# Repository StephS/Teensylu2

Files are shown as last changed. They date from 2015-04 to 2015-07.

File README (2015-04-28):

This board is a PROTOTYPE until the design is built and tested.

Version 0.9 is ready for production, earlier versions should not be used.

Please see Teensylu2_Pin_Map.htm for the correct pin mapping using the teensyduino library. Analog pins should use the analog pin reference.

The BOM is included. Please use parts of the same or higher ratings.

If you'd like to donate so I can buy the full version of Eagle, and make more cool stuff, please contact me through Google+

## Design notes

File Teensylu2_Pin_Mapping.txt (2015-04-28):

Package Pin Number	Pin Name	Teensyduino Pin Number	Connected NET	Description
1	PE6	18	Z-STOP	Z Endstop or Z probe input
2	PE7	19	PE7	Not Connected
9	PE3		PE3	Not Connected
10	PB0	20	SDCS	SDCS
11	PB1	21	SCLK	SCLK
12	PB2	22	MOSI	MOSI
13	PB3	23	MISO	MISO
14	PB4	24	PB4	Extension Header PIN 5
15	PB5	25	Y-STOP	Y Endstop
16	PB6	26	X-STOP	X Endstop
17	PB7	27	SCDCD	SD Card Detect
18	PE4	36	E-STOP	E Endstop
19	PE5	37	PE5	Extension Header PIN 4
25	PD0	0	PD0-SCL	Extension Header PIN 6
26	PD1	1	PD1-SDA	Extension Header PIN 7
27	PD2	2	PD2-RX1	Extension Header PIN 8
28	PD3	3	PD3-TX1	Extension Header PIN 9
29	PD4	4	PD4	Extension Header PIN 10
30	PD5	5	PD5	Extension Header PIN 11
31	PD6	6	PD6	Extension Header PIN 12
32	PD7	7	PD7	Extension Header PIN 13
33	PE0	8	E2-STEP	2nd Extruder STEP pin
34	PE1	9	E2-DIR	2nd Extruder DIR pin
35	PC0	10	!E2-ENABLE	2nd Extruder ENABLE pin
36	PC1	11	E1-STEP	1st Extruder STEP pin
37	PC2	12	E1-DIR	1st Extruder DIR pin
38	PC3	13	!E1-ENABLE	1st Extruder ENABLE pin
39	PC4	14	!HOTBED	Hot Bed Mosfet control pin
40	PC5	15	!HOTEND-1	Hot End 1 Mosfet control pin
41	PC6	16	!PWM-FAN	Fan Mosfet control pin
42	PC7	17	Z-STEP	Z Axis STEP pin
43	PE2		PE2	Boot Mode pin
44	PA7	35	Z-DIR	Z Axis DIR pin
45	PA6	34	!Z-ENABLE	Z Axis ENABLE pin
46	PA5	33	Y-STEP	Y Axis STEP pin
47	PA4	32	Y-DIR	Y Axis DIR pin
48	PA3	31	!Y-ENABLE	Y Axis ENABLE pin
49	PA2	30	X-STEP	X Axis STEP pin
50	PA1	29	X-DIR	X Axis DIR pin
51	PA0	28	!X-ENABLE	X Axis ENABLE pin
54	PF7	45	A7	Extension Header PIN 14
55	PF6	44	A6	Not Connected
56	PF5	43	A5	Not Connected
57	PF4	42	A4	Not Connected
58	PF3	41	!HOTEND-2	Hot End 2 Mosfet control pin
59	PF2	40	E2-THERM	Hot End 2 thermistor input pin
60	PF1	39	E1-THERM	Hot End 1 thermistor input pin
61	PF0	38	B-THERM	Hot Bed thermistor input pin

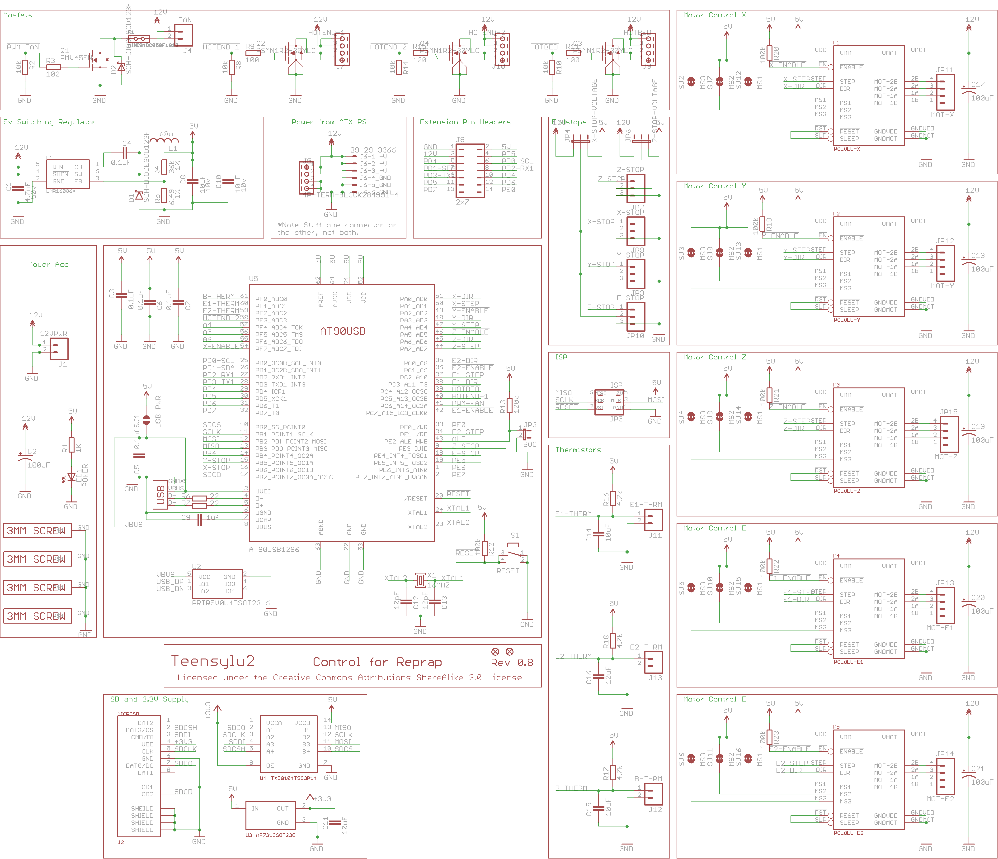
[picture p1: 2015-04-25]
Teensylu2_Schematic.png

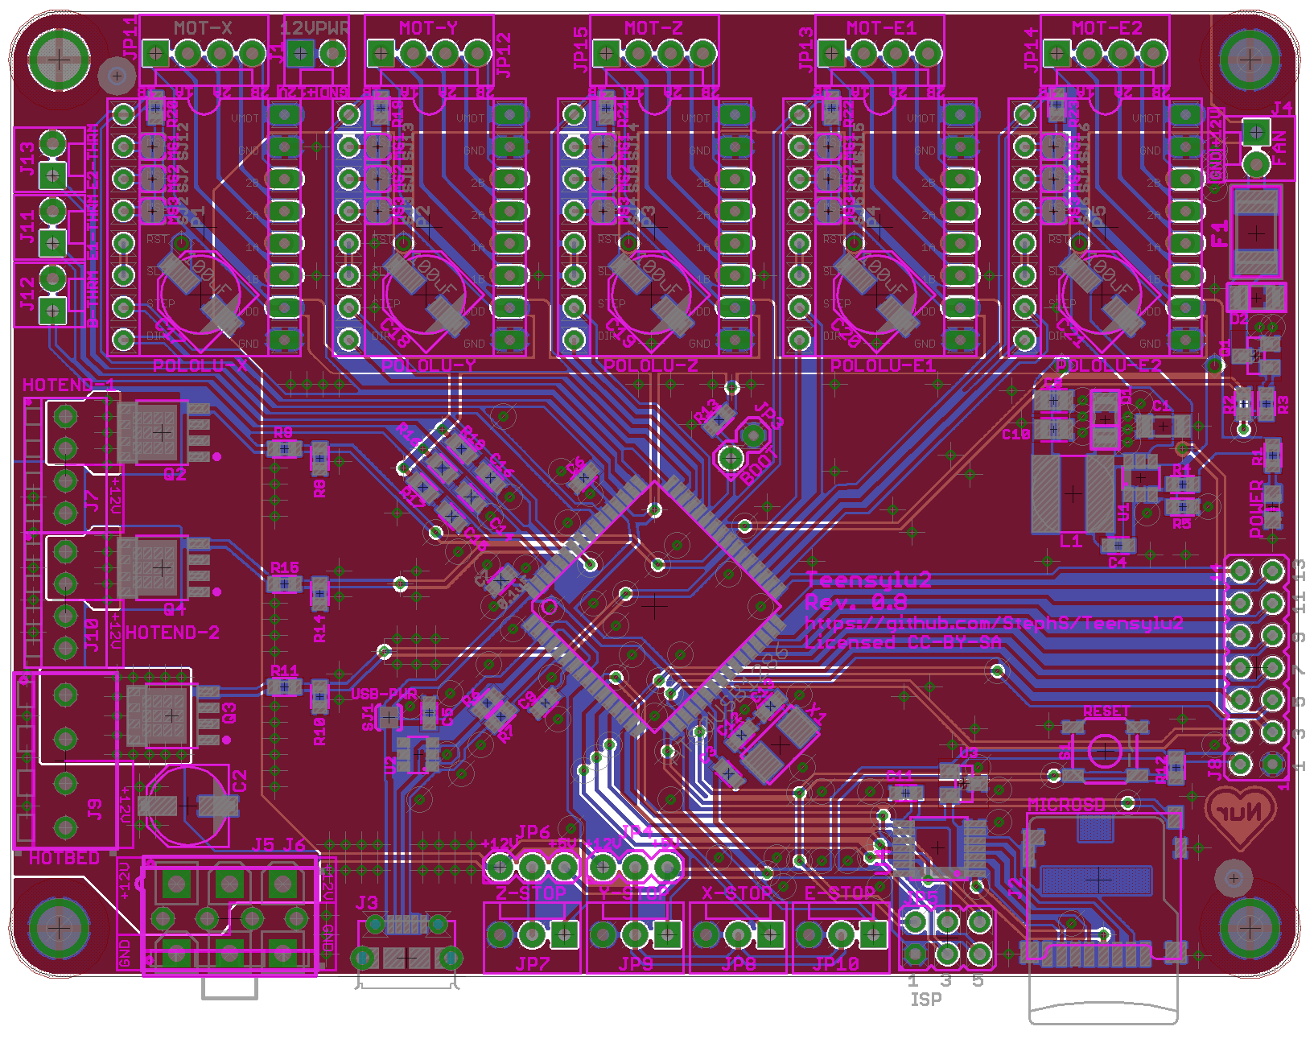
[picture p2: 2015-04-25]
Teensylu2_Board.png

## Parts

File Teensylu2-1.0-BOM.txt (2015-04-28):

Partlist exported from C:/Users/stshalt/Documents/Teensylu2/Teensylu2-0.9.sch at 4/28/2015 11:14:26 AM

Qty Value                 Device                     Package             Parts                             Description                                  CURRENT DCR   DESCRIPTION                      ESR    INDUCTANCE IRMS MANUFACTURER            MANUFACTURER_PART_NUMBER      NOTES                                                                       RDS_ON   REVERSE_VOLTAGE TOLERANCE VDC VGS   VOLTAGE VOLTAGE_OUTPUT
4   0.1uF                 CAPACITOR_0603             CAPC1608X92N        C3, C5, C6, C7                                                                                                                                       Murata                  GRM188R71C104KA01D                                                                                                                 10%       16V                             
1   0.1uF                 CAPACITOR_0603             CAPC1608X92N        C4                                                                                                                                                   Samsung                 CL10B104KB8NNNC                                                                                                                    10%       50V                             
4   100                   RESISTOR_0603              RESC1608X55N        R3, R9, R11, R15                                                                                                                                                                                                                                                                                                                                          
7   100k                  RESISTOR_0603              RESC1608X55N        R12, R13, R19, R20, R21, R22, R23                                                                                                                                                                                                                                                                                                                         
6   100uF                 CPOL-USD                   PANASONIC_D         C2, C17, C18, C19, C20, C21       POLARIZED CAPACITOR, American symbol                                                                               Panasonic               EEE-FTH101XAP                                                                                                                      20%       50v                             
4   10k                   RESISTOR_0603              RESC1608X55N        R2, R8, R10, R14                                                                                                                                                                                                                                                                                                                                          
2   10pF                  CAPACITOR_0603             CAPC1608X92N        C12, C13                                                                                                                                             Samsung                 CL10C100JB8NCNC                                                                                                                    5%        50V                             
4   10uF                  CAPACITOR_0603             CAPC1608X92N        C11, C14, C15, C16                                                                                                                                   Murata                  GRM188R61C106MA73D                                                                                                                 20%       16V                             
2   10uF                  CAPACITOR_0805             CAPC2012X145AN      C8, C10                                                                                                                       0.0030                 Murata                  GRM21BR71A106KE51L                                                                                                                 10%       10v                             
1   16MHZ                 XTAL                       NDK-XTAL            X1                                                                                                                                                   NDK                     NX5032GA-16.000000MHZ-LN-CD-1                                                                                                                                                
1   1K                    RESISTOR_0603              RESC1608X55N        R1                                                                                                                                                                                                                                                                                                                                                        
1   1uF                   CAPACITOR_0603             CAPC1608X92N        C9                                                                                                                                                   Samsung                 CL10A105MO8NNNC                                                                                                                    20%       16V                             
2   22                    RESISTOR_0603              RESC1608X55N        R6, R7                                                                                                                                                                                                                                                                                                                                                    
1   2x7                   JP7Q                       JP7Q                J8                                JUMPER                                                     DIL VERTICAL PC TAIL PIN HEADER                         Harwin                  M20-9980746                                                                                                                                                                  
1   36k                   RESISTOR_0603              RESC1608X55N        R4                                                                                                                                                                                                                                                                                                              1%                                        
1   39-29-3066            39-29-3066                 39-29-3066          J6                                Mini FIT connector 6 pol Without Snap-in peg                                                                       Molex                   0039293066                                                                                                                                                                   
4   3MM-SCREW             3MM-SCREW                  PLATEDSCREW         SCREW1, SCREW2, SCREW3, SCREW4    3mm Plated Through Hole Screw                                                                                                                                                                                                                                                                                           
3   4.7k                  RESISTOR_0603              RESC1608X55N        R16, R17, R18                                                                                                                                                                                                                                                                                                                                             
1   4.7uF                 CAPACITOR_1206             CAPC3215X168N       C1                                                                                                                                                   Yaiyo Yuden             UMK316AB7475KL-T                                                                                                                   10%       50v                             
1   4P-TERM-BLOCK284391-4 4P-TERM-BLOCK284391-4      284391-4            J5                                                                             12A                                                                   TE Connectivity         284391-4                                                                                                                                                                     
1   6.49k                 RESISTOR_0603              RESC1608X55N        R5                                                                                                                                                                                                                                                                                                              1%                                        
1   68uH                  INDUCTORSRN6045            SRN6045             L1                                                                             900mA   0.351                                         68uH       0.9A Bourns                  SRN6045-680M                                                                                                                                                                 
1   AP7313SOT23C          AP7313SOT23C               SOT23C              U3                                                                             150mA         IC REG LDO 3.3V 0.15A SOT23-3                           Diodes Incorporated     AP7313-33SAG-7                                                                                                                                                 3.3V          
1   AT90USB1286           AT90USB                    TQFP64-2            U5                                                                                                                                                   Atmel                   AT90USB1286                                                                                                                                                                  
1   BOOT                  JUMPER-2PTH                1X02                JP3                               Jumper                                                     SIL VERTICAL PC TAIL PIN HEADER                         Harwin                  M20-9990246                                                                                                                                                                  
2   FIDUCIAL1X2.5         FIDUCIAL1X2.5              FIDUCIAL-1X2.5      JP1, JP2                          Fiducial Alignment Points                                                                                                                                                                                                                                                                                               
1   HOTBED                4P-TERM-BLOCK284391-4      284391-4            J9                                                                             12A                                                                   TE Connectivity         284391-4                                                                                                                                                                     
1   HOTEND-1              4P-TERM-BLOCK282834-4      282834-4            J7                                                                             10A                                                                   TE Connectivity         282834-4                                                                                                                                                                     
1   HOTEND-2              4P-TERM-BLOCK282834-4      282834-4            J10                                                                            10A                                                                   TE Connectivity         282834-4                                                                                                                                                                     
1   ISP                   PROGHEADER                 ISP                 JP5                               JUMPER                                                                                                                                                                                                                                                                                                                  
2   JUMPER-3PTH           JUMPER-3PTH                1X03                JP4, JP6                                                                                                                                                                                                                                                                                                                                                  
1   LMR16006X             LMR16006X                  TSOT6               U1                                Texas Instruments LMR16006XDDCT              600mA                                                                 Texas Instruments       LMR16006XDDCT                                                                                                                                                                
5   M02POLAR              M02POLAR                   MOLEX-1X2           J1, J4, J11, J12, J13             Header 2                                                   CONN HEADER 2POS .100 VERT TIN                          Molex                   0022272021                    Can use alternative part for Right Angle. MFG: TE Connectivity PN: 640455-2                                                                    
4   M03POLAR              M03POLAR                   MOLEX-1X3           JP7, JP8, JP9, JP10               Header 3                                                   CONN HEADER 3POS .100 VERT TIN                          Molex                   0022272031                    Can use alternative part for Right Angle. MFG: TE Connectivity PN: 640455-3                                                                    
1   MICROSD               MICROSD                    AMPHENOL-MICROSD    J2                                                                                           CONN MICRO SD CARD PUSH-PULL R/A                        Amphenol                114-00841-68                                                                                                                                                                 
1   MINISMDC050F1812      MINISMDC050F1812           MINISMDC            F1                                                                             0.5A                                                                  TE Connectivity         MINISMDC050F-2                                                                                                                                                               
1   MMUN2211LT3G          TRANSISTOR_NPN_BIASSOT23C  SOT23C              Q5                                Transistor NPN                                             TRANS PREBIAS NPN 246MW SOT23-3                         ON Semiconductor        MMUN2211LT3G                                                                                                                                                                 
1   MOT-E1                M04POLAR                   MOLEX-1X4           JP13                              Header 4                                                   CONN HEADER 4POS .100 VERT TIN                          Molex                   0022272041                    Can use alternative part for Right Angle. MFG: TE Connectivity PN: 640455-4                                                                    
1   MOT-E2                M04POLAR                   MOLEX-1X4           JP14                              Header 4                                                   CONN HEADER 4POS .100 VERT TIN                          Molex                   0022272041                    Can use alternative part for Right Angle. MFG: TE Connectivity PN: 640455-4                                                                    
1   MOT-X                 M04POLAR                   MOLEX-1X4           JP11                              Header 4                                                   CONN HEADER 4POS .100 VERT TIN                          Molex                   0022272041                    Can use alternative part for Right Angle. MFG: TE Connectivity PN: 640455-4                                                                    
1   MOT-Y                 M04POLAR                   MOLEX-1X4           JP12                              Header 4                                                   CONN HEADER 4POS .100 VERT TIN                          Molex                   0022272041                    Can use alternative part for Right Angle. MFG: TE Connectivity PN: 640455-4                                                                    
1   MOT-Z                 M04POLAR                   MOLEX-1X4           JP15                              Header 4                                                   CONN HEADER 4POS .100 VERT TIN                          Molex                   0022272041                    Can use alternative part for Right Angle. MFG: TE Connectivity PN: 640455-4                                                                    
5   MS1                   SOLDERJUMPER-NCSJ-TRACE    SJ_2S-TRACE         SJ12, SJ13, SJ14, SJ15, SJ16                                                                                                                                                                                                                                                                                                                              
5   MS2                   SOLDERJUMPER-NCSJ-TRACE    SJ_2S-TRACE         SJ7, SJ8, SJ9, SJ10, SJ11                                                                                                                                                                                                                                                                                                                                 
5   MS3                   SOLDERJUMPER-NCSJ-TRACE    SJ_2S-TRACE         SJ2, SJ3, SJ4, SJ5, SJ6                                                                                                                                                                                                                                                                                                                                   
1   PMV45EN               MOSFET-NCH_SOT-23          SOT23C              Q1                                                                             1.2A                                                                  International Rectifier IRLML2060TRPBF                                                                                                                                         60V                   
1   POLOLU-E1             POLOLU-ALLEGRO             POLOLU-STEPPER-PTH  P4                                                                                                                                                                                                                                                                                                                                                        
1   POLOLU-E2             POLOLU-ALLEGRO             POLOLU-STEPPER-PTH  P5                                                                                                                                                                                                                                                                                                                                                        
1   POLOLU-X              POLOLU-ALLEGRO             POLOLU-STEPPER-PTH  P1                                                                                                                                                                                                                                                                                                                                                        
1   POLOLU-Y              POLOLU-ALLEGRO             POLOLU-STEPPER-PTH  P2                                                                                                                                                                                                                                                                                                                                                        
1   POLOLU-Z              POLOLU-ALLEGRO             POLOLU-STEPPER-PTH  P3                                                                                                                                                                                                                                                                                                                                                        
1   POWER                 LEDCHIPLED_0805            CHIPLED_0805        LED1                              LED                                                                                                                Kingbright              APT2012SGC                                                                                                                                                                   
1   PRTR5V0U4DSOT23-6     PRTR5V0U4DSOT23-6          SOT23-6             U2                                NXP Semiconductors PRTR5V0U4D,125                                                                                  NXP Semiconductors      PRTR5V0U4D,125                                                                                                                                                               
3   PSMN1R2-30YLC         PSMN1R2-30YLCPOWERPACK-S08 LFPACK-POWERPAK-SO8 Q2, Q3, Q4                        N-Channel MOSFET - 30V 100A LFPAK            100A                                                                  NXP Semiconductors      PSMN1R2-30YLC,115                                                                                         1.25mOhm                               1.95V 30V                   
1   RESET                 TAC_SWITCHSMD              TACTILE_SWITCH_SMD  S1                                Momentary Switch                                                                                                   Bourns                  7914J-1-000E                                                                                                                                                                 
2   SCH-DIODESOD123F      SCH-DIODESOD123F           SOD123F             D1, D2                            Schottky Diodes                              1A                                                                    NXP Semiconductors      PMEG4010CEH,115                                                                                                    40V                                                       
1   TXB0104TSSOP14        TXB0104TSSOP14             TSSOP14             U4                                                                                           IC VOLT-LEVEL TRANSLATOR 14TSSOP                        Texas Instruments       TXB0104PWR                                                                                                                                                                   
1   USB-MICRO-PTH         USB-MICRO-PTH              USB-MICROB-PTH      J3                                USB Connectors                                                                                                     FCI                     10118194-0001LF                                                                                                                                                              
1   USB-PWR               SOLDERJUMPERNO             SJ_2S-NO            SJ1                               Solder Jumper

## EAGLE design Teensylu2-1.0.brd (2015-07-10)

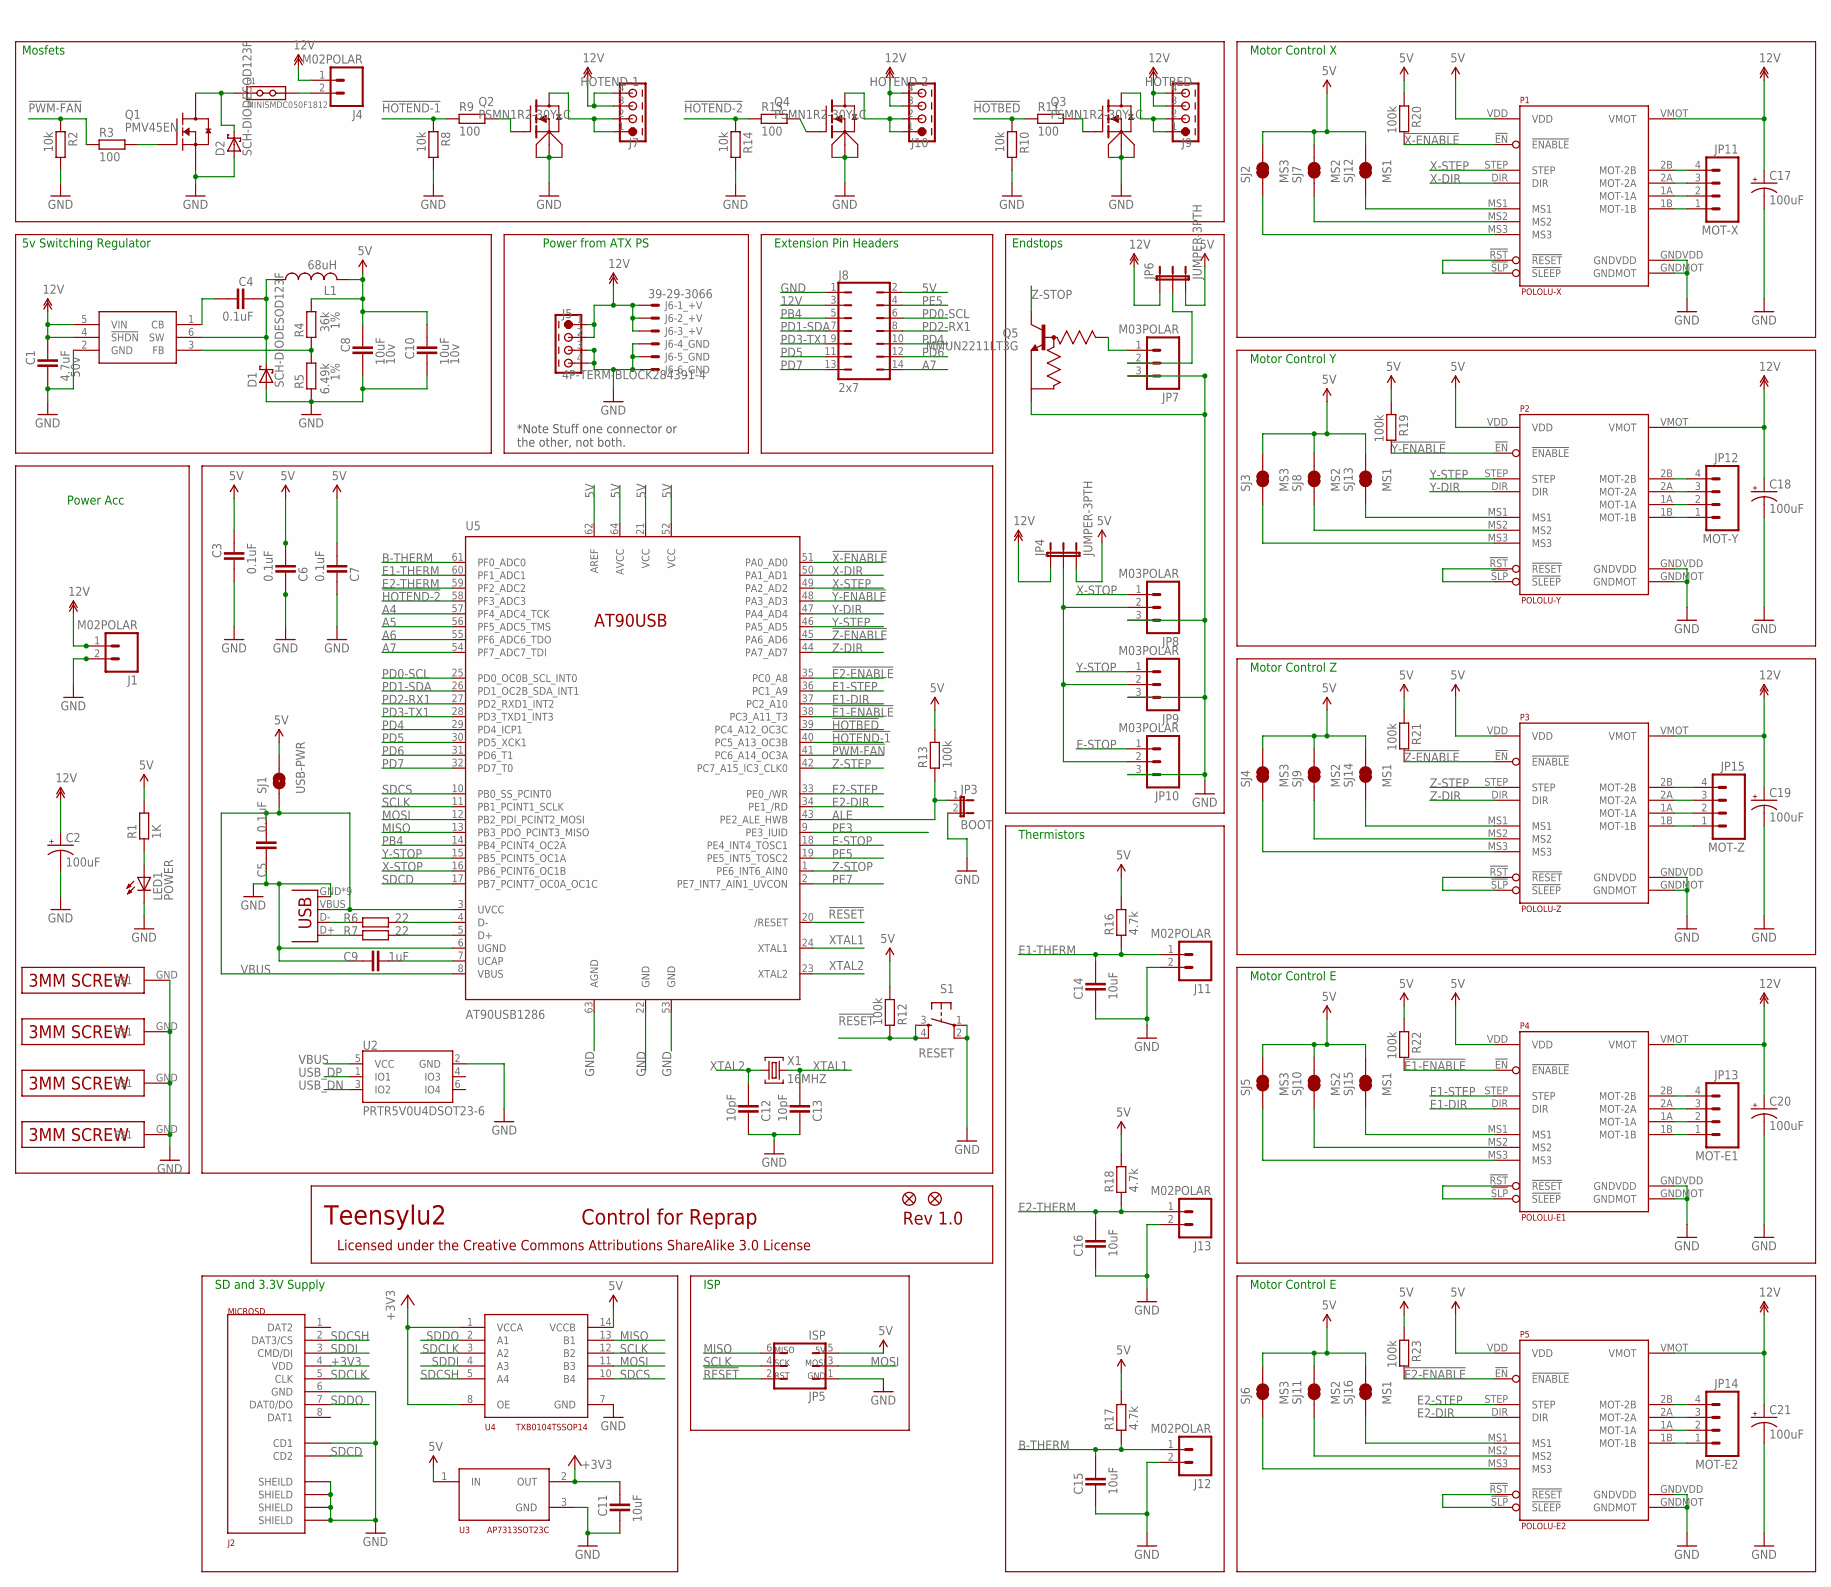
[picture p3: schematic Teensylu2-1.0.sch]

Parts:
C1: 4.7uF; CAPC3215X168N; TOLERANCE 10%; MANUFACTURER_PART_NUMBER UMK316AB7475KL-T
C2, C17, C18, C19, C20, C21: 100uF; PANASONIC_D; TOLERANCE 20%; MANUFACTURER_PART_NUMBER EEE-FTH101XAP
C3, C5, C6, C7: 0.1uF; CAPC1608X92N; TOLERANCE 10%; MANUFACTURER_PART_NUMBER GRM188R71C104KA01D
C4: 0.1uF; CAPC1608X92N; TOLERANCE 10%; MANUFACTURER_PART_NUMBER CL10B104KB8NNNC
C8, C10: 10uF; CAPC2012X145AN; TOLERANCE 10%; MANUFACTURER_PART_NUMBER GRM21BR71A106KE51L
C9: 1uF; CAPC1608X92N; TOLERANCE 20%; MANUFACTURER_PART_NUMBER CL10A105MO8NNNC
C11, C14, C15, C16: 10uF; CAPC1608X92N; TOLERANCE 20%; MANUFACTURER_PART_NUMBER GRM188R61C106MA73D
C12, C13: 10pF; CAPC1608X92N; TOLERANCE 5%; MANUFACTURER_PART_NUMBER CL10C100JB8NCNC
D1: SCH-DIODESOD123F; SOD123F; MANUFACTURER_PART_NUMBER PMEG4010CEH,115
D2: SCH-DIODESOD123F; SOD123F
F1: MINISMDC050F1812; MINISMDC
J1, J4, J11, J12, J13: M02POLAR; MOLEX-1X2; MANUFACTURER_PART_NUMBER 0022272021
J2: MICROSD; AMPHENOL-MICROSD
J3: USB-MICRO-PTH; USB-MICROB-PTH
J5: 4P-TERM-BLOCK284391-4; 284391-4
J6: 39-29-3066
J7: HOTEND-1; 282834-4
J8: 2x7; JP7Q; MANUFACTURER_PART_NUMBER M20-9980746
J9: HOTBED; 284391-4
J10: HOTEND-2; 282834-4
JP1, JP2: FIDUCIAL1X2.5; FIDUCIAL-1X2.5
JP3: BOOT; 1X02; MANUFACTURER_PART_NUMBER M20-9990246
JP4, JP6: JUMPER-3PTH; 1X03
JP5: ISP
JP7, JP8, JP9, JP10: M03POLAR; MOLEX-1X3; MANUFACTURER_PART_NUMBER 0022272031
JP11: MOT-X; MOLEX-1X4
JP12: MOT-Y; MOLEX-1X4
JP13: MOT-E1; MOLEX-1X4
JP14: MOT-E2; MOLEX-1X4
JP15: MOT-Z; MOLEX-1X4
L1: 68uH; SRN6045; MANUFACTURER_PART_NUMBER SRN6045-680M
LED1: POWER; CHIPLED_0805; MANUFACTURER_PART_NUMBER APT2012SGC
P1: POLOLU-X; POLOLU-STEPPER-PTH
P2: POLOLU-Y; POLOLU-STEPPER-PTH
P3: POLOLU-Z; POLOLU-STEPPER-PTH
P4: POLOLU-E1; POLOLU-STEPPER-PTH
P5: POLOLU-E2; POLOLU-STEPPER-PTH
Q1: PMV45EN; SOT23C; VOLTAGE 60V; MANUFACTURER_PART_NUMBER IRLML2060TRPBF
Q2, Q3, Q4: PSMN1R2-30YLC; LFPACK-POWERPAK-SO8
Q5: MMUN2211LT3G; SOT23C; MANUFACTURER_PART_NUMBER MMUN2211LT3G
R1: 1K; RESC1608X55N
R2, R8, R10, R14: 10k; RESC1608X55N
R3, R9, R11, R15: 100; RESC1608X55N
R4: 36k; RESC1608X55N; TOLERANCE 1%
R5: 6.49k; RESC1608X55N; TOLERANCE 1%
R6, R7: 22; RESC1608X55N
R12, R13, R19, R20, R21, R22, R23: 100k; RESC1608X55N
R16, R17, R18: 4.7k; RESC1608X55N
S1: RESET; TACTILE_SWITCH_SMD
SCREW1, SCREW2, SCREW3, SCREW4: 3MM-SCREW; PLATEDSCREW
SJ1: USB-PWR; SJ_2S-NO
SJ2, SJ3, SJ4, SJ5, SJ6: MS3; SJ_2S-TRACE
SJ7, SJ8, SJ9, SJ10, SJ11: MS2; SJ_2S-TRACE
SJ12, SJ13, SJ14, SJ15, SJ16: MS1; SJ_2S-TRACE
U1: LMR16006X; TSOT6
U2: PRTR5V0U4DSOT23-6; SOT23-6
U3: AP7313SOT23C; SOT23C
U4: TXB0104TSSOP14; TSSOP14
U5: AT90USB1286; TQFP64-2; MANUFACTURER_PART_NUMBER AT90USB1286
X1: 16MHZ; NDK-XTAL; MANUFACTURER_PART_NUMBER NX5032GA-16.000000MHZ-LN-CD-1

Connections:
5V: C3.1, C6.2, C7.2, C8.1, C10.1, J8.2, JP4.3, JP5.5, JP6.3, L1.2, P1.VDD, P2.VDD, P3.VDD, P4.VDD, P5.VDD, R1.2, R4.1, R12.2, R13.2, R16.2, R17.2, R18.2, R19.1, R20.1, R21.1, R22.1, R23.1, SJ1.2, SJ2.2, SJ3.2, SJ4.2, SJ5.2, SJ6.2, SJ7.2, SJ8.2, SJ9.2, SJ10.2, SJ11.2, SJ12.2, SJ13.2, SJ14.2, SJ15.2, SJ16.2, U3.1 (IN), U4.14 (VCCB), U5.21 (VCC), U5.52 (VCC), U5.62 (AREF), U5.64 (AVCC)
5VREG_CB: C4.2, U1.1 (CB)
5VREG_FB: R4.2, R5.1, U1.3 (FB)
5VREG_SW: C4.1, D1.C, L1.1, U1.6 (SW)
12V: C1.1, C2.+, C17.+, C18.+, C19.+, C20.+, C21.+, J1.1, J4.1, J5.1, J5.2, J6.1, J6.2, J6.3, J7.3, J7.4, J8.3, J9.3, J9.4, J10.3, J10.4, JP4.1, JP6.1, P1.VMOT, P2.VMOT, P3.VMOT, P4.VMOT, P5.VMOT, U1.4 (!SHDN), U1.5 (VIN)
!E1-ENABLE: P4.!EN (!ENABLE), R22.2, U5.38 (PC3_A11_T3)
!E2-ENABLE: P5.!EN (!ENABLE), R23.2, U5.35 (PC0_A8)
!HOTBED: R10.1, R11.1, U5.39 (PC4_A12_OC3C)
!HOTEND-1: R8.1, R9.1, U5.40 (PC5_A13_OC3B)
!HOTEND-2: R14.1, R15.1, U5.58 (PF3_ADC3)
!PWM-FAN: R2.1, R3.1, U5.41 (PC6_A14_OC3A)
!RESET: JP5.2, R12.1, S1.3, S1.4, U5.20 (/RESET)
!X-ENABLE: P1.!EN (!ENABLE), R20.2, U5.51 (PA0_AD0)
!Y-ENABLE: P2.!EN (!ENABLE), R19.2, U5.48 (PA3_AD3)
!Z-ENABLE: P3.!EN (!ENABLE), R21.2, U5.45 (PA6_AD6)
+3V3: C11.1, J2.4 (VDD), U3.2 (OUT), U4.1 (VCCA), U4.8 (OE)
A4: U5.57 (PF4_ADC4_TCK)
A5: U5.56 (PF5_ADC5_TMS)
A6: U5.55 (PF6_ADC6_TDO)
A7: J8.14, U5.54 (PF7_ADC7_TDI)
ALE: JP3.1, R13.1, U5.43 (PE2_ALE_HWB)
B-THERM: C15.2, J12.1, R17.1, U5.61 (PF0_ADC0)
E1-DIR: P4.DIR, U5.37 (PC2_A10)
E1-STEP: P4.STEP, U5.36 (PC1_A9)
E1-THERM: C14.2, J11.1, R16.1, U5.60 (PF1_ADC1)
E2-DIR: P5.DIR, U5.34 (PE1_/RD)
E2-MOT-1A: JP14.2, P5.1A (MOT-1A)
E2-MOT-1B: JP14.1, P5.1B (MOT-1B)
E2-MOT-2A: JP14.3, P5.2A (MOT-2A)
E2-MOT-2B: JP14.4, P5.2B (MOT-2B)
E2-STEP: P5.STEP, U5.33 (PE0_/WR)
E2-THERM: C16.2, J13.1, R18.1, U5.59 (PF2_ADC2)
E-MOT-1A: JP13.2, P4.1A (MOT-1A)
E-MOT-1B: JP13.1, P4.1B (MOT-1B)
E-MOT-2A: JP13.3, P4.2A (MOT-2A)
E-MOT-2B: JP13.4, P4.2B (MOT-2B)
E-MS1: P4.MS1, SJ15.1
E-MS2: P4.MS2, SJ10.1
E-MS3: P4.MS3, SJ5.1
E-MS4: P5.MS1, SJ16.1
E-MS5: P5.MS2, SJ11.1
E-MS6: P5.MS3, SJ6.1
E-RESETSLEEP: P4.!RST (!RESET), P4.!SLP (!SLEEP)
E-RESETSLEEP1: P5.!RST (!RESET), P5.!SLP (!SLEEP)
E-STOP: JP10.1, U5.18 (PE4_INT4_TOSC1)
ENDSTOP+V: JP4.2, JP8.2, JP9.2, JP10.2
GND: C1.2, C2.-, C3.2, C5.1, C6.1, C7.1, C8.2, C9.1, C10.2, C11.2, C12.1, C13.1, C14.1, C15.1, C16.1, C17.-, C18.-, C19.-, C20.-, C21.-, D1.A, D2.A, J1.2, J2.6 (GND), J2.C1 (SHEILD), J2.C2 (SHIELD), J2.C3 (SHIELD), J2.C4 (SHIELD), J2.CD1, J3.GND, J3.GND1 (GND), J3.GND2 (GND), J3.GND3 (GND), J3.GND4 (GND), J3.GND5 (GND), J3.GND6 (GND), J3.GND7 (GND), J3.GND8 (GND), J5.3, J5.4, J6.4, J6.5, J6.6, J8.1, J11.2, J12.2, J13.2, JP3.2, JP5.1, JP7.3, JP8.3, JP9.3, JP10.3, LED1.C, P1.GNDMOT, P1.GNDVDD, P2.GNDMOT, P2.GNDVDD, P3.GNDMOT, P3.GNDVDD, P4.GNDMOT, P4.GNDVDD, P5.GNDMOT, P5.GNDVDD, Q1.2 (S), Q2.1 (S1), Q2.2 (S2), Q2.3 (S3), Q3.1 (S1), Q3.2 (S2), Q3.3 (S3), Q4.1 (S1), Q4.2 (S2), Q4.3 (S3), Q5.2 (E), R2.2, R5.2, R8.2, R10.2, R14.2, S1.1, S1.2, SCREW1.GND, SCREW2.GND, SCREW3.GND, SCREW4.GND, U1.2 (GND), U2.2 (GND), U3.3 (GND), U4.7 (GND), U5.6 (UGND), U5.22 (GND), U5.53 (GND), U5.63 (AGND)
HOTBED-GND: J9.1, J9.2, Q3.5-8 (D)
HOTEND-GND: J7.1, J7.2, Q2.5-8 (D)
HOTEND-GND1: J10.1, J10.2, Q4.5-8 (D)
MISO: JP5.6, U4.13 (B1), U5.13 (PB3_PDO_PCINT3_MISO)
MOSI: JP5.3, U4.11 (B3), U5.12 (PB2_PDI_PCINT2_MOSI)
unnamed: LED1.A, R1.1
unnamed: Q3.4 (G), R11.2
unnamed: R6.2, U5.4 (D-)
unnamed: R7.2, U5.5 (D+)
unnamed: F1.P$2, J4.2
unnamed: D2.C, F1.P$1, Q1.3 (D)
unnamed: Q1.1 (G), R3.2
unnamed: Q2.4 (G), R9.2
unnamed: Q4.4 (G), R15.2
PB4: J8.5, U5.14 (PB4_PCINT4_OC2A)
PD0-SCL: J8.6, U5.25 (PD0_OC0B_SCL_INT0)
PD1-SDA: J8.7, U5.26 (PD1_OC2B_SDA_INT1)
PD2-RX1: J8.8, U5.27 (PD2_RXD1_INT2)
PD3-TX1: J8.9, U5.28 (PD3_TXD1_INT3)
PD4: J8.10, U5.29 (PD4_ICP1)
PD5: J8.11, U5.30 (PD5_XCK1)
PD6: J8.12, U5.31 (PD6_T1)
PD7: J8.13, U5.32 (PD7_T0)
PE3: U5.9 (PE3_IUID)
PE5: J8.4, U5.19 (PE5_INT5_TOSC2)
PE7: U5.2 (PE7_INT7_AIN1_UVCON)
SCLK: JP5.4, U4.12 (B2), U5.11 (PB1_PCINT1_SCLK)
SDCD: J2.CD2, U5.17 (PB7_PCINT7_OC0A_OC1C)
SDCLK: J2.5 (CLK), U4.3 (A2)
SDCS: U4.10 (B4), U5.10 (PB0_SS_PCINT0)
SDCSH: J2.2 (DAT3/CS), U4.5 (A4)
SDDI: J2.3 (CMD/DI), U4.4 (A3)
SDDO: J2.7 (DAT0/DO), U4.2 (A1)
UCAP: C9.2, U5.7 (UCAP)
USB_DN: J3.D-, R6.1, U2.3 (IO2)
USB_DP: J3.D+, R7.1, U2.1 (IO1)
VBUS: C5.2, J3.VBUS, SJ1.1, U2.5 (VCC), U5.3 (UVCC), U5.8 (VBUS)
X-DIR: P1.DIR, U5.50 (PA1_AD1)
X-MOT-1A: JP11.2, P1.1A (MOT-1A)
X-MOT-1B: JP11.1, P1.1B (MOT-1B)
X-MOT-2A: JP11.3, P1.2A (MOT-2A)
X-MOT-2B: JP11.4, P1.2B (MOT-2B)
X-MS1: P1.MS1, SJ12.1
X-MS2: P1.MS2, SJ7.1
X-MS3: P1.MS3, SJ2.1
X-RESETSLEEP: P1.!RST (!RESET), P1.!SLP (!SLEEP)
X-STEP: P1.STEP, U5.49 (PA2_AD2)
X-STOP: JP8.1, U5.16 (PB6_PCINT6_OC1B)
XTAL1: C13.2, U5.24 (XTAL1), X1.P$2 (2)
XTAL2: C12.2, U5.23 (XTAL2), X1.P$1 (1)
Y-DIR: P2.DIR, U5.47 (PA4_AD4)
Y-MOT-1A: JP12.2, P2.1A (MOT-1A)
Y-MOT-1B: JP12.1, P2.1B (MOT-1B)
Y-MOT-2A: JP12.3, P2.2A (MOT-2A)
Y-MOT-2B: JP12.4, P2.2B (MOT-2B)
Y-MS1: P2.MS1, SJ13.1
Y-MS2: P2.MS2, SJ8.1
Y-MS3: P2.MS3, SJ3.1
Y-RESETSLEEP: P2.!RST (!RESET), P2.!SLP (!SLEEP)
Y-STEP: P2.STEP, U5.46 (PA5_AD5)
Y-STOP: JP9.1, U5.15 (PB5_PCINT5_OC1A)
Z-DIR: P3.DIR, U5.44 (PA7_AD7)
Z-MOT-1A: JP15.2, P3.1A (MOT-1A)
Z-MOT-1B: JP15.1, P3.1B (MOT-1B)
Z-MOT-2A: JP15.3, P3.2A (MOT-2A)
Z-MOT-2B: JP15.4, P3.2B (MOT-2B)
Z-MS1: P3.MS1, SJ14.1
Z-MS2: P3.MS2, SJ9.1
Z-MS3: P3.MS3, SJ4.1
Z-RESETSLEEP: P3.!RST (!RESET), P3.!SLP (!SLEEP)
Z-STEP: P3.STEP, U5.42 (PC7_A15_IC3_CLK0)
Z-STOP: Q5.3 (C), U5.1 (PE6_INT6_AIN0)
Z-STOP-BIAS: JP7.1, Q5.1 (B)
Z-STOP-SUPPLY: JP6.2, JP7.2

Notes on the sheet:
Motor Control X
Motor Control Y
Motor Control Z
Motor Control E
ISP
Thermistors
Endstops
Mosfets
Power Acc
Teensylu2
Rev 1.0
Control for Reprap
Licensed under the Creative Commons Attributions ShareAlike 3.0 License
Extension Pin Headers
Power from ATX PS
5v Switching Regulator
SD and 3.3V Supply
*Note Stuff one connector or the other, not both.

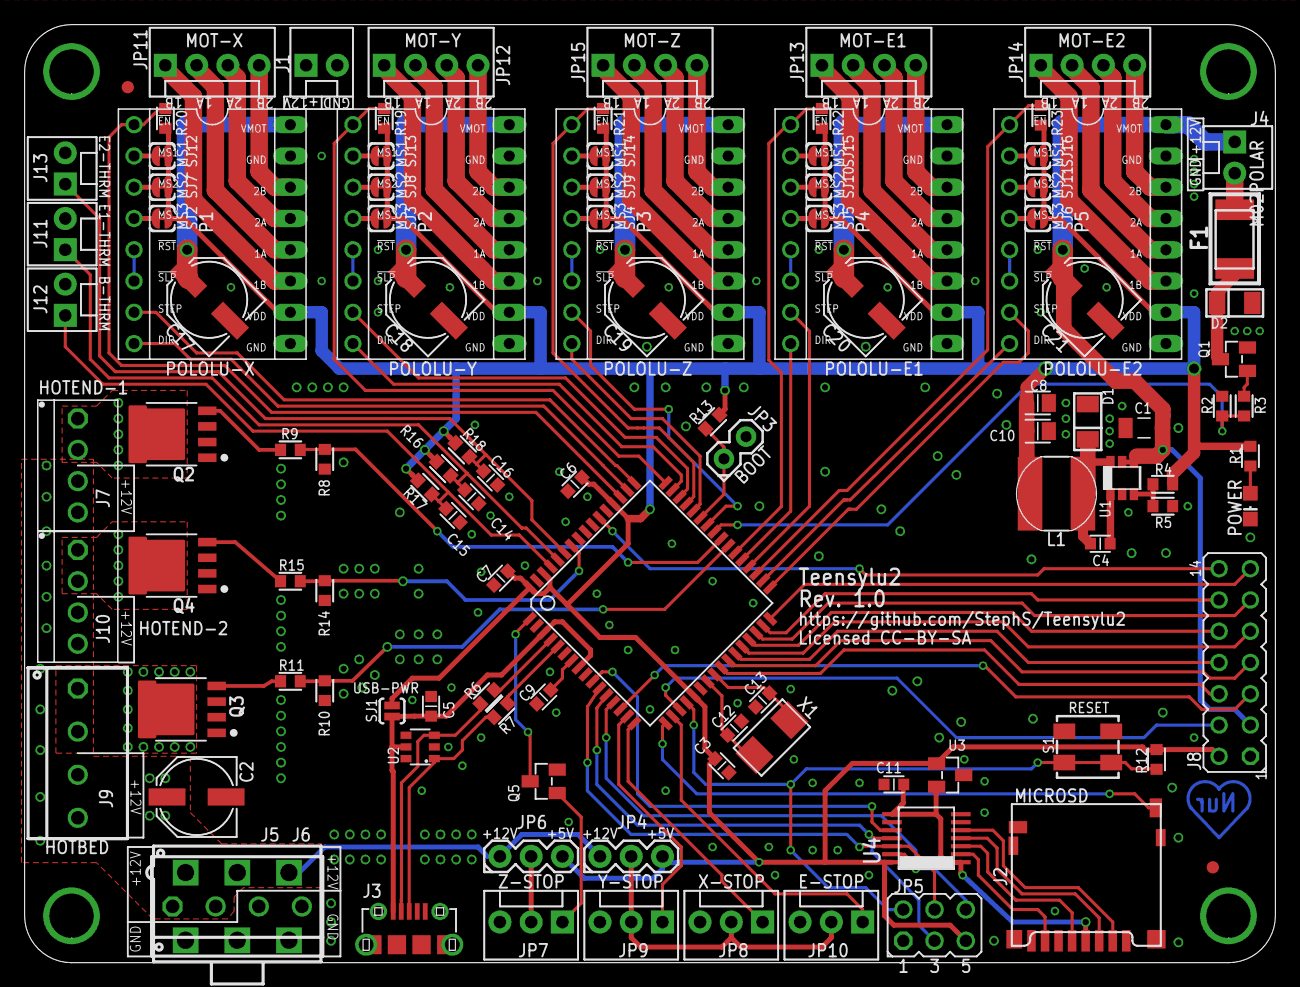
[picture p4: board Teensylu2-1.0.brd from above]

Board: 2 copper layers, 101.6 x 76.2 mm, 114 parts (0 on the bottom side), 116 nets.

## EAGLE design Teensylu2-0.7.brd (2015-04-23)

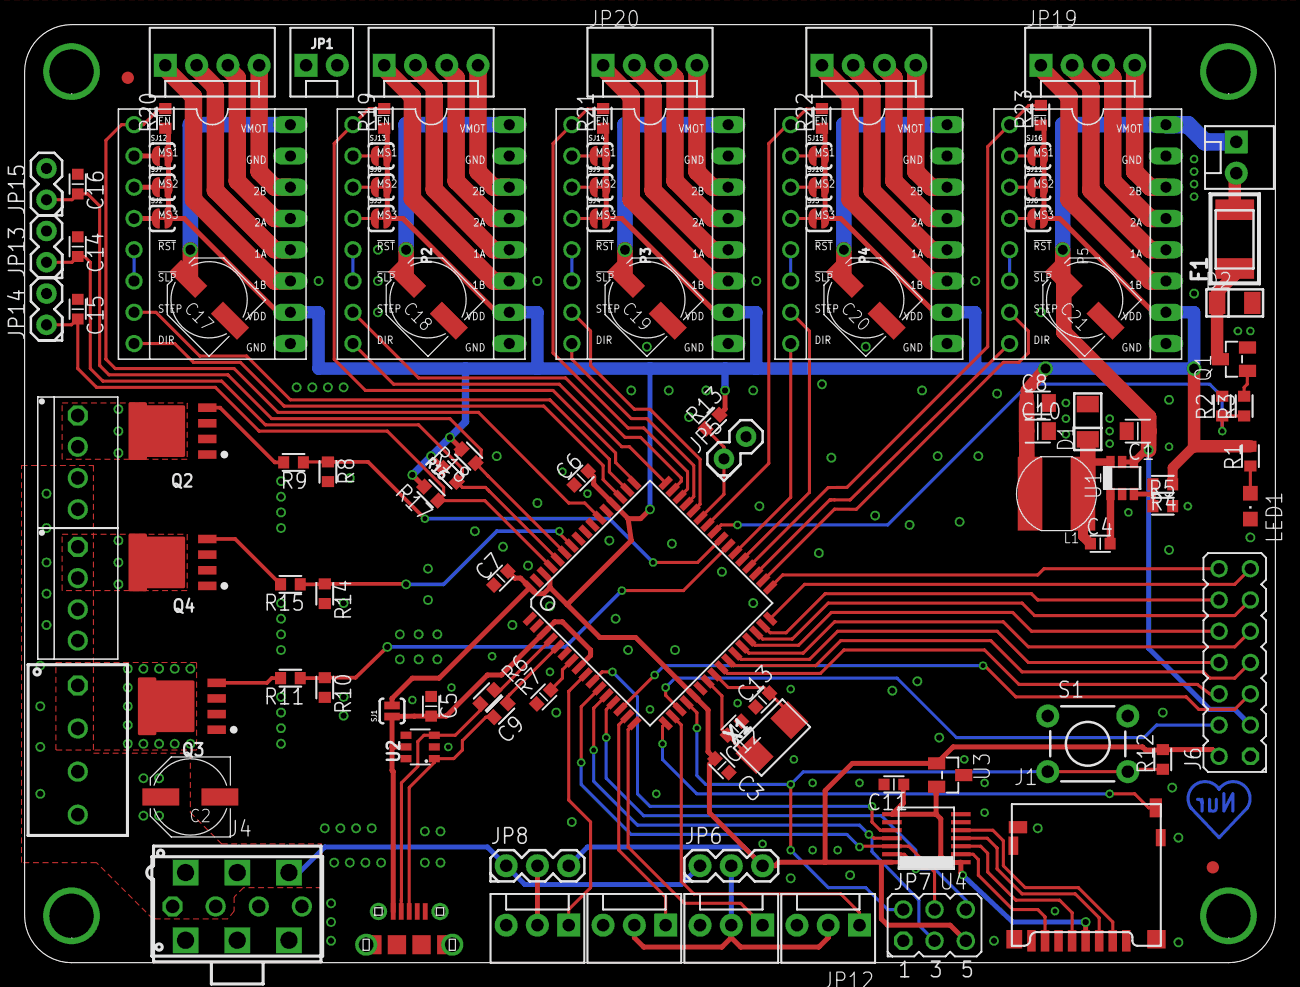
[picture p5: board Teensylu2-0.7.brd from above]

Board: 2 copper layers, 101.6 x 76.2 mm, 113 parts (0 on the bottom side), 115 nets.

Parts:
C1: 4.7uF; CAPC2012X145AN
C2, C17, C18, C19, C20, C21: 100uF; PANASONIC_D
C3, C6, C7: 0.1uF; CAPC1608X92N
C4: 100nF; CAPC1608X92N
C5: 0.1uf; CAPC1608X92N
C8, C10: 10uF; CAPC2012X145AN
C9: 1uf; CAPC1608X92N
C11, C14, C15, C16: 10uF; CAPC1608X92N
C12, C13: 10pF; CAPC1608X92N
D1, D2: SCH-DIODESOD123F; SOD123F
F1: MINISMDC050F1812; MINISMDC
IC1: AT90USB1286; TQFP64-2
J1: MICROSD; AMPHENOL-MICROSD
J2: USB-MICRO-PTH; USB-MICROB-PTH
J3, J7: 4P-TERM-BLOCK284391-4; 284391-4
J4: 39-29-3066
J5, J8: 4P-TERM-BLOCK282834-4; 282834-4
J6: 2x7; JP7Q
JP1: 12VPWR; MOLEX-1X2
JP2: FAN; MOLEX-1X2
JP3, JP4: FIDUCIAL1X2.5; FIDUCIAL-1X2.5
JP5: BOOT; 1X02
JP6, JP8: JUMPER-3PTH; 1X03
JP7: ISP
JP9: Z-STOP; MOLEX-1X3
JP10: X-STOP; MOLEX-1X3
JP11: Y-STOP; MOLEX-1X3
JP12: E-STOP; MOLEX-1X3
JP13, JP14, JP15: 1X02
JP16: MOT-X; MOLEX-1X4
JP17: MOT-Y; MOLEX-1X4
JP18, JP19: MOT-E; MOLEX-1X4
JP20: MOT-Z; MOLEX-1X4
L1: 68uH; SRN6045
LED1: CHIPLED_0805
P1: POLOLU-X; POLOLU-STEPPER-PTH
P2: POLOLU-Y; POLOLU-STEPPER-PTH
P3: POLOLU-Z; POLOLU-STEPPER-PTH
P4, P5: POLOLU-E; POLOLU-STEPPER-PTH
Q1: PMV45EN; SOT23C
Q2, Q3, Q4: PSMN1R2-30YLCPOWERPACK-S08; LFPACK-POWERPAK-SO8
R1: 1K; RESC1608X55N
R2, R8, R10, R14: 10k; RESC1608X55N
R3, R9, R11, R15: 100; RESC1608X55N
R4: 36k; RESC1608X55N
R5: 6.49; RESC1608X55N
R6, R7: 22; RESC1608X55N
R12, R13, R19, R20, R21, R22, R23: 100k; RESC1608X55N
R16, R17, R18: 4.7k; RESC1608X55N
S1: RESET; TACTILE-PTH
SCREW1, SCREW2, SCREW3, SCREW4: 3MM-SCREW; PLATEDSCREW
SJ1: SOLDERJUMPERNO; SJ_2S-NO
SJ2, SJ3, SJ4, SJ5, SJ6, SJ7, SJ8, SJ9, SJ10, SJ11, SJ12, SJ13, SJ14, SJ15, SJ16: SOLDERJUMPER-NCSJ-TRACE; SJ_2S-TRACE
U1: LMR16006X; TSOT6
U2: PRTR5V0U4DSOT23-6; SOT23-6
U3: AP7313SOT23C; SOT23C
U4: TXB0104TSSOP14; TSSOP14
X1: 16MHZ; NDK-XTAL

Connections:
5V: C3.1, C6.2, C7.2, C8.1, C10.1, IC1.21, IC1.52, IC1.62, IC1.64, J6.2, JP6.3, JP7.5, JP8.3, L1.2, P1.VDD, P2.VDD, P3.VDD, P4.VDD, P5.VDD, R1.2, R4.1, R12.2, R13.2, R16.2, R17.2, R18.2, R19.1, R20.1, R21.1, R22.1, R23.1, SJ1.2, SJ2.2, SJ3.2, SJ4.2, SJ5.2, SJ6.2, SJ7.2, SJ8.2, SJ9.2, SJ10.2, SJ11.2, SJ12.2, SJ13.2, SJ14.2, SJ15.2, SJ16.2, U3.1, U4.14
5VREG_CB: C4.2, U1.1
5VREG_FB: R4.2, R5.1, U1.3
5VREG_SW: C4.1, D1.C, L1.1, U1.6
12V: C1.1, C2.+, C17.+, C18.+, C19.+, C20.+, C21.+, J3.1, J3.2, J4.1, J4.2, J4.3, J5.3, J5.4, J6.3, J7.3, J7.4, J8.3, J8.4, JP1.1, JP2.1, JP6.1, JP8.1, P1.VMOT, P2.VMOT, P3.VMOT, P4.VMOT, P5.VMOT, U1.4, U1.5
!E1-ENABLE: IC1.42, P4.!EN, R22.2
!E2-ENABLE: IC1.36, P5.!EN, R23.2
!HOTBED: IC1.39, R10.1, R11.1
!HOTEND-1: IC1.40, R8.1, R9.1
!HOTEND-2: IC1.58, R14.1, R15.1
!PWM-FAN: IC1.41, R2.1, R3.1
!RESET: IC1.20, JP7.2, R12.1, S1.3, S1.4
!X-ENABLE: IC1.54, P1.!EN, R20.2
!Y-ENABLE: IC1.49, P2.!EN, R19.2
!Z-ENABLE: IC1.46, P3.!EN, R21.2
+3V3: C11.1, J1.4, U3.2, U4.1, U4.8
ALE: IC1.43, JP5.1, R13.1
B-THERM: C15.2, IC1.61, JP14.1, R17.1
E1-DIR: IC1.38, P4.DIR
E1-STEP: IC1.37, P4.STEP
E1-THERM: C14.2, IC1.60, JP13.1, R16.1
E2-DIR: IC1.35, P5.DIR
E2-STEP: IC1.34, P5.STEP
E2-THERM: C16.2, IC1.59, JP15.1, R18.1
E-MOT-1A: JP18.2, P4.1A
E-MOT-1A1: JP19.2, P5.1A
E-MOT-1B: JP18.1, P4.1B
E-MOT-1B1: JP19.1, P5.1B
E-MOT-2A: JP18.3, P4.2A
E-MOT-2A1: JP19.3, P5.2A
E-MOT-2B: JP18.4, P4.2B
E-MOT-2B1: JP19.4, P5.2B
E-MS1: P4.MS1, SJ15.1
E-MS2: P4.MS2, SJ10.1
E-MS3: P4.MS3, SJ5.1
E-MS4: P5.MS1, SJ16.1
E-MS5: P5.MS2, SJ11.1
E-MS6: P5.MS3, SJ6.1
E-RESETSLEEP: P4.!RST, P4.!SLP
E-RESETSLEEP1: P5.!RST, P5.!SLP
E-STOP: IC1.18, JP12.1
ENDSTOP+V: JP6.2, JP10.2, JP11.2, JP12.2
GND: C1.2, C2.-, C3.2, C5.1, C6.1, C7.1, C8.2, C9.1, C10.2, C11.2, C12.1, C13.1, C14.1, C15.1, C16.1, C17.-, C18.-, C19.-, C20.-, C21.-, D1.A, D2.A, IC1.6, IC1.22, IC1.53, IC1.63, J1.6, J1.C1, J1.C2, J1.C3, J1.C4, J1.CD1, J2.GND, J2.GND1, J2.GND2, J2.GND3, J2.GND4, J2.GND5, J2.GND6, J2.GND7, J2.GND8, J3.3, J3.4, J4.4, J4.5, J4.6, J6.1, JP1.2, JP5.2, JP7.1, JP9.3, JP10.3, JP11.3, JP12.3, JP13.2, JP14.2, JP15.2, LED1.C, P1.GNDMOT, P1.GNDVDD, P2.GNDMOT, P2.GNDVDD, P3.GNDMOT, P3.GNDVDD, P4.GNDMOT, P4.GNDVDD, P5.GNDMOT, P5.GNDVDD, Q1.2, Q2.1, Q2.2, Q2.3, Q3.1, Q3.2, Q3.3, Q4.1, Q4.2, Q4.3, R2.2, R5.2, R8.2, R10.2, R14.2, S1.1, S1.2, SCREW1.GND, SCREW2.GND, SCREW3.GND, SCREW4.GND, U1.2, U2.2, U3.3, U4.7
HOTBED-GND: J7.1, J7.2, Q3.5-8
HOTEND-GND: J5.1, J5.2, Q2.5-8
HOTEND-GND1: J8.1, J8.2, Q4.5-8
MISO: IC1.13, JP7.6, U4.13
MOSI: IC1.12, JP7.3, U4.11
unnamed: LED1.A, R1.1
unnamed: Q3.4, R11.2
unnamed: IC1.4, R6.2
unnamed: IC1.5, R7.2
unnamed: F1.P$2, JP2.2
unnamed: D2.C, F1.P$1, Q1.3
unnamed: Q1.1, R3.2
unnamed: Q2.4, R9.2
unnamed: Q4.4, R15.2
PB4: IC1.14, J6.5
PD0-SCL: IC1.25, J6.6
PD1-SDA: IC1.26, J6.7
PD2-RX1: IC1.27, J6.8
PD3-TX1: IC1.28, J6.9
PD4: IC1.29, J6.10
PD5: IC1.30, J6.11
PD6: IC1.31, J6.12
PD7: IC1.32, J6.13
PE0: IC1.33, J6.14
PE5: IC1.19, J6.4
SCLK: IC1.11, JP7.4, U4.12
SDCD: IC1.17, J1.CD2
SDCLK: J1.5, U4.3
SDCS: IC1.10, U4.10
SDCSH: J1.2, U4.5
SDDI: J1.3, U4.4
SDDO: J1.7, U4.2
UCAP: C9.2, IC1.7
USB_DN: J2.D-, R6.1, U2.3
USB_DP: J2.D+, R7.1, U2.1
VBUS: C5.2, IC1.3, IC1.8, J2.VBUS, SJ1.1, U2.5
X-DIR: IC1.51, P1.DIR
X-MOT-1A: JP16.2, P1.1A
X-MOT-1B: JP16.1, P1.1B
X-MOT-2A: JP16.3, P1.2A
X-MOT-2B: JP16.4, P1.2B
X-MS1: P1.MS1, SJ12.1
X-MS2: P1.MS2, SJ7.1
X-MS3: P1.MS3, SJ2.1
X-RESETSLEEP: P1.!RST, P1.!SLP
X-STEP: IC1.50, P1.STEP
X-STOP: IC1.16, JP10.1
XTAL1: C13.2, IC1.24, X1.P$2
XTAL2: C12.2, IC1.23, X1.P$1
Y-DIR: IC1.48, P2.DIR
Y-MOT-1A: JP17.2, P2.1A
Y-MOT-1B: JP17.1, P2.1B
Y-MOT-2A: JP17.3, P2.2A
Y-MOT-2B: JP17.4, P2.2B
Y-MS1: P2.MS1, SJ13.1
Y-MS2: P2.MS2, SJ8.1
Y-MS3: P2.MS3, SJ3.1
Y-RESETSLEEP: P2.!RST, P2.!SLP
Y-STEP: IC1.47, P2.STEP
Y-STOP: IC1.15, JP11.1
Z-DIR: IC1.45, P3.DIR
Z-MOT-1A: JP20.2, P3.1A
Z-MOT-1B: JP20.1, P3.1B
Z-MOT-2A: JP20.3, P3.2A
Z-MOT-2B: JP20.4, P3.2B
Z-MS1: P3.MS1, SJ14.1
Z-MS2: P3.MS2, SJ9.1
Z-MS3: P3.MS3, SJ4.1
Z-RESETSLEEP: P3.!RST, P3.!SLP
Z-STEP: IC1.44, P3.STEP
Z-STOP: IC1.9, JP9.1
Z-STOP-SUPPLY: JP8.2, JP9.2

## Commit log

2015-04-22 Initial Teensylu2 commit, version 0.6
    This version is untested, and still needs the silkscreen updated, and a
    BOM built. DO NOT USE FOR PRODUCTION.
    [Teensylu2-0.6.brd, Teensylu2-0.6.sch]
2015-04-23 Alpha release
    Caps have been moved over to SMD. Almost have all parts in the Teensylu
    lib. Silkscreen is still incomplete. Switched to a new regulator. Added
    attributes to all of the parts (haven't done all of the resistors yet,
    but most others should have info like the manufacturer part #, etc.)
    [Teensylu2-0.6.brd, Teensylu2-0.7.brd, Teensylu2-0.7.sch]
2015-04-24 Beta Release
    This is a BETA release. The design is pending review.
    Changes:
    Added more via's to the Mosfets. Silkscreen is complete. Reset button
    changed to SMD. Moved endstop voltage selector. Capacitors are now all
    SMD. Teensylu lib should contain all of the components.
    [Teensylu2-0.7.sch, Teensylu2-0.8.brd, Teensylu2-0.8.sch]
2015-04-25 Updated BOM
    Added a BOM, changed C1 to 1206 package.
    [Teensylu2-0.8.brd, Teensylu2-0.8.sch]
2015-04-25 Adding screenshots
    Screenshots of the board and schematic.
2015-04-28 Production release
    Pin mapping is added. Had to move a lot of pins around due to limitation
    of the Teensyduino library.
    [Teensylu2-0.9.brd, Teensylu2-0.9.sch]
2015-07-10 Fixed Z Endstop
    Collector and Emitter were swapped.
    [Teensylu2-1.0.brd, Teensylu2-1.0.sch]

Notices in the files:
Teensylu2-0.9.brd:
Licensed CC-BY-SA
